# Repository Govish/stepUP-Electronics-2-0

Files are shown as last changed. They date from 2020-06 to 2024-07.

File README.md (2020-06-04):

# stepUP-Electronics-2-0
 New Electronics Suite for the stepUP 3D Printer!
 New Electronics include:
  - An updated LCD control panel loosely based off the Panelolu2
  - New printer mainboard
     - Arduino DUE printer controller running Marlin 2.0
     - ESP32 acting as WiFi server through ESP3D
     - Multiplexed SD card allowing read/write access to both the ESP32 and the Arduino DUE
     - TMC2130 Stepper Drivers with SPI configuration and connected diagnostic pins
     - RGB LED light strip control
     - High-power 20A heated bed control
     - ATX PSU control
  - Black ribbon cable wiring all throughout the machine with PCB breakouts
     - Full connectorization

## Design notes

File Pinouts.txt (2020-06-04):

 ======== LCD Connector =======
			 =========
	No Connect	-| 1   2 |- 	Ground
	Encoder B	-| 3   4 |-	LED Red
	Encoder A	-| 5   6 |-	LED Green
	Buffer SCL	-| 7   8 |-	LED Blue
	Buffer SDA	-| 9  10 |-	5V
			 =========

 ======== Encoder Daughterboard =======
			 =========
	VCC		-| 1   2 |- 	Ground
	Encoder B	-| 3   4 |-	LED Blue
	Encoder A	-| 5   6 |-	LED Green
	Encoder Switch	-| 7   8 |-	LED Red
			 =========

 ======== Y-Axis Motor/Runout Sensor Breakout ========
			 =========
	Motor 1B	-| 1   2 |-	Motor 1A
	Runout A	-| 3   4 |-	Runout B
	Motor 2B	-| 5   6 |-	Motor 2A
			 =========

 ======== Z-Axis Motor/Endstop Breakout ========
			 =========
	Motor 1B	-| 1   2 |-	Motor 1A
	Endstop A	-| 3   4 |-	Endstop B
	Motor 2B	-| 5   6 |-	Motor 2A
			 =========

 ======== LED Endstop Breakout ========
			 =========
	Blue		-| 1   2 |-	Green
	12V		-| 3   4 |-	Red
	Endstop A	-| 5   6 |-	Endstop B
			 =========

 ======== Heatbed Breakout ========
			 =========
	Thermistor A	-| 1   2 |-	Thermistor B
	Heater (-)	-| 3   4 |-	Heater (+)
	Heater (-)	-| 5   4 |-	Heater (+)
	Heater (-)	-| 7   4 |-	Heater (+)
	Heater (-)	-| 9   4 |-	Heater (+)
	Heater (-)	-| 11 12 |-	Heater (+)
	Heater (-)	-| 13 14 |-	Heater (+)
	Heater (-)	-| 15 16 |-	Heater (+)
	Heater (-)	-| 17 18 |-	Heater (+)
	Heater (-)	-| 19 20 |-	Heater (+)
	Heater (-)	-| 21 22 |-	Heater (+)
	Heater (-)	-| 23 24 |-	Heater (+)
	Heater (-)	-| 25 26 |-	Heater (+)
			 =========

 ======== Gantry Breakout (to controller) ========
			 =========
	Ext 2A		-| 1   2 |-	Ext 1A
	Ext 2B		-| 3   4 |-	Ext 1B
	+12V		-| 5   4 |-	Print Fan (-)
	+12V		-| 7   4 |-	Hotend Fan (-)
	+12V		-| 9   4 |-	Thermistor A
	Heater (-)	-| 11 12 |-	Thermistor B
	Heater (-)	-| 13 14 |-	Endstop A
	Heater (-)	-| 15 16 |-	Endstop B
	X 1B		-| 17 18 |-	X 2B
	X 1A		-| 19 20 |-	X 2A
			 =========

 ======== Gantry Breakout (to extruder) ========
			 =========
	Ext 2A		-| 1   2 |-	Ext 1A
	Ext 2B		-| 3   4 |-	Ext 1B
	Heater (-)	-| 5   4 |-	Print Fan (-)
	Heater (-)	-| 7   4 |-	Hotend Fan (-)
	Heater (-)	-| 9   4 |-	Thermistor A
	+12V		-| 11 12 |-	Thermistor B
	+12V		-| 13 14 |-	Endstop A
	+12V		-| 15 16 |-	Endstop B
			 =========

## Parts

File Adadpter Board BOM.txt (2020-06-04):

IDC-6  Connector: III
IDC-16 Connector: II
IDC-20 Connector: I
IDC-26 Connector: I

JST-4: IIIII
JST-2: IIIIIII
Screw Terminal (0.1"): I 

XT60: I
XT30: I

SMD LED: III
SMD LED RES: III

RGB ENCODER: I

USB-A Connector: I

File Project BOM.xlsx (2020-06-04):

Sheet: All Together
Package | Quantity | Price @Break | Total Price | Value | Manufacturer | Part Number | Supplier (DigiKey) P/N | Notes for Substitution | Qty on Hand | Qty to Buy | Buy Prices
Nonstandard | 4 | $0.22 | $0.88 | Fuseholder_ATM | Keystone Electronics | 3557 | 36-3557-ND | Match footprint if exists? | 0 | 5 | $1.10
02x03 P2.54mm | 6 | $0.45 | $2.70 | IDC-6 | Wurth Electronik | 61200621621 | 732-5394-ND | IDC6, Match Footprint | 0 | 7 | $3.15
02x05 P2.54mm | 1 | $0.45 | $0.45 | IDC-10 | Wurth Electronik | 61201021621 | 732-2094-ND | IDC10, Match Footprint | 0 | 2 | $0.90
02x08 P2.54mm | 2 | $0.59 | $1.18 | IDC-16 | Wurth Electronik | 61201621621 | 732-2095-ND | IDC16, Match Footprint | 0 | 3 | $1.77
02x10 P2.54mm | 2 | $0.89 | $1.78 | IDC-20 | Wurth Electronik | 61202021621 | 732-2096-ND | IDC20, Match Footprint | 0 | 3 | $2.67
02x13 P2.54mm | 2 | $1.04 | $2.08 | IDC-26 | Wurth Electronik | 61202621621 | 732-2097-ND | IDC26, Match Footprint | 0 | 3 | $3.12
Nonstandard | 1 | $1.22 | $1.22 | USB_A | CNC Tech | 1001-008B-01001 | 1175-1608-ND | Match footprint if exists? | 0 | 2 | $2.44
0603 | 5 | $0.18 | $0.90 | Red | Wurth Electronik | 150060RS55040 | 732-12015-1-ND | Match Package and Color | 0 | 6 | $1.08
0603 | 4 | $0.18 | $0.72 | Green | Wurth Electronik | 150060VS55040 | 732-12017-1-ND | Match Package and Color | 0 | 5 | $0.90
0603 | 6 | $0.18 | $1.08 | Yellow | Wurth Electronik | 150060YS55040 | 732-12018-1-ND | Match Package and Color | 0 | 7 | $1.26
1206 Reverse Mount | 1 | $0.18 | $0.18 | Red | Wurth Electronik | 156120RS75000 | 732-5030-1-ND | Match Footprint | 0 | 2 | $0.36
1206 Reverse Mount | 1 | $0.18 | $0.18 | Green | Wurth Electronik | 156120VS75000 | 732-5032-1-ND | Match Footprint | 0 | 2 | $0.36
1206 Reverse Mount | 1 | $0.18 | $0.18 | Yellow | Wurth Electronik | 156120YS75000 | 732-5034-1-ND | Match Footprint | 0 | 2 | $0.36
Nonstandard | 1 | $3.69 | $3.69 | Socket_SD | TE Connectivity AMP Connectors | 2041021-4 | A101492CT-ND | Match footprint if exists? | 0 | 2 | $7.38
TSSOP-8 4.4x3 P0.65) | 1 | $0.80 | $0.80 | 24LC256 | Microchip | 24LC256-I/ST | 24LC256-I/ST-ND | Match pinout, greater or equal capacity | 0 | 2 | $1.60
Screw_Term 2.54mm | 1 | $0.92 | $0.92 | - | TE Connectivity AMP Connectors | 282834-2 | A98333-ND | Match Pitch, Footprint | 0 | 2 | $1.84
02x05 SMD Pin Header | 1 | $0.58 | $0.58 | - | CNC Tech | 3020-10-0300-00 | 1175-1621-ND | IDC Format, Match Footprint | 0 | 1 | $0.58
02x04 P2.54mm | 1 | $2.40 | $2.40 | - | TE Connectivity AMP Connectors | 5-534998-4 | A32954-ND | 5-7mm Insulation Height | 0 | 1 | $2.40
SSOP-14 (5.3x6.2 P0.65) | 1 | $0.64 | $0.64 | 74HC4066 | Nexperia | 74HC4066DB,112 | 1727-6100-ND | Match Footprint, 4066 family | 0 | 2 | $1.28
Arduino Mega/Due | 1 | $37.40 | $37.40 | - | Arduino | A000062 | 1050-1049-ND | Requires desoldering of input DC connector (clearance) | 0 | 1 | $37.40
Nonstandard | 1 | $0.24 | $0.24 | 10A | OptiFuse | APM-10A | 2298-APM-10A-ND | Any 10A ATM Fuse | 0 | 2 | $0.48
Nonstandard | 1 | $0.24 | $0.24 | 25A | OptiFuse | APM-25A | 2298-APM-25A-ND | Any 25A ATM Fuse | 0 | 2 | $0.48
01x02 P2.5 | 8 | $0.15 | $1.20 | JST-2 | JST Sales America | B2B-XH-A(LF)(SN) | 455-2247-ND | Amazon Link (https://www.amazon.com/gp/product/B015Y6JOUG/ref=ox_sc_act_title_5?smid=AYI27JSX7SHMW&psc=1) | 20 | 0 | $0.00
01x04 P2.5 | 7 | $0.21 | $1.47 | JST-4 | JST Sales America | B4B-XH-A(LF)(SN) | 455-2249-ND | Amazon Link (https://www.amazon.com/gp/product/B015Y6JOUG/ref=ox_sc_act_title_5?smid=AYI27JSX7SHMW&psc=1) | 20 | 0 | $0.00
SMC | 1 | $0.32 | $0.32 | 80V 3A Schottky | Comchip Technology | CDBC380-G | 641-1123-1-ND | 3A, 50V Rated or more, Match Footprint | 0 | 2 | $0.64
0603 | 23 | $0.00 | $0.00 | 100n | Samsung Electromechanics | CL10B10KB8NNNC | 1276-1000-1-ND | 50V Rated X5R or better | 70 | 0 | $0.00
0603 | 1 | $0.03 | $0.03 | 270p | Samsung Electromechanics | CL10B271KB8NNNC | 1276-2019-1-ND | Check PSU design doc for voltage rating | 0 | 10 | $0.34
0603 | 1 | $0.03 | $0.03 | 4.7n | Samsung Electromechanics | CL10B472KB8NFNC | 1276-2064-1-ND | Check PSU design doc for voltage rating | 0 | 10 | $0.34
0603 | 1 | $0.04 | $0.04 | 10p | Samsung Electromechanics | CL10C100CB8NNNC | 1276-1069-1-ND | Check PSU design doc for voltage rating | 0 | 10 | $0.38
0805 | 6 | $0.00 | $0.00 | 4u7 | Samsung Electromechanics | CL21A475KPFNNNE | 1276-1259-1-ND | 10V Rated X5R or better | 9 | 0 | $0.00
SOD-123F | 33 | $0.13 | $4.42 | 50V 1A Fast Recovery | SMC Diode Solutions | DSS15UTR | 1655-1928-1-ND | >50V, 1A; Match Footprint | 0 | 40 | $5.36
CP_Radial (D12.5mm P5.00mm) | 6 | $0.24 | $1.44 | 470u | Panasonic Electronic Components | EEU-FM1H471 | P12400-ND | Match or better: voltage, high freq Iripple, impedance | 0 | 7 | $1.68
Nonstandard | 1 | $0.00 | $0.00 | - | Espressif Systems | ESP32 Core Board V2 | - | Possible pin-compatible options, match footprint | 1 | 0 | $0.00
VSSOP-8 (3.0x3.0 P0.65) | 1 | $2.14 | $2.14 | LM3488 | Texas Instruments | LM3488MMX/NOPB | 296-35417-1-ND | Different Packaging Possible | 0 | 2 | $4.28
SMDIP-4 (W9.53mm) | 3 | $0.45 | $1.35 | LTV-817S | Lite-on Inc | LTV-817S | 160-1367-5-ND | Match Footprint and Pinout; Iout > 50mA | 0 | 4 | $1.80
TSSOP-14 (4.4x5 P0.65) | 1 | $0.36 | $0.36 | 74HC14 | ON Semiconductor | MC74HC14ADTR2G | MC74HC14ADTR2GOSCT-ND | Match Footprint, 7414 family | 0 | 2 | $0.72
SSOP-28 (5.3x10.2_P0.65) | 1 | $1.26 | $1.26 | MCP23017 | Microchip Technology | MCP23017T-E/SS | MCP23017T-E/SSCT-ND | No Substitutes, but similar versions should be alright | 0 | 2 | $2.52
SOD-323 | 11 | $0.12 | $1.35 | 3.6V | ON Semiconductor | MM3Z3V6T1G | MM3Z3V6T1GOSCT-ND | Match Package and Voltage | 0 | 15 | $1.84
SOT-23 | 8 | $0.28 | $2.24 | - | ON Semiconductor | NTR3C21NZT1G | NTR3C21NZT1GOSCT-ND | >20V, >3.6A to ambient, >8V Vgs, Logic Level | 0 | 12 | $3.36
TO-252 | 4 | $0.89 | $3.56 | - | ON Semiconductor | NVD5C668NLT4G | NVD5C668NLT4GOSCT-ND | >50V, <10mOhm, <30nC gate charge, TO-252 | 0 | 6 | $5.34
SOIC-8 (3.9x4.9 P1.27) | 2 | $1.86 | $3.72 | P82B715 | Texas Instruments | P82B715DRG4 | 296-52682-1-ND | Similar part from NXP (https://www.digikey.com/product-detail/en/nxp-usa-inc/P82B715TD-112/568-3981-5-ND/739477) | 0 | 3 | $5.58
SSOP-8 (2.95x2.8 P0.65) | 1 | $0.67 | $0.67 | PCA9306 | Texas Instruments | PCA9306DCTR | 296-18509-1-ND | Match Footprint and Pinout | 0 | 2 | $1.34
2512 | 1 | $0.59 | $0.59 | 7mR | Yageo | PE2512FKE7W0R007L | YAG2161CT-ND | Match Footprint; 1% or better | 0 | 2 | $1.18
Nonstandard | 1 | $6.18 | $6.18 | RGB Encoder | Bourns | PEL12T-4225S-S1024 | PEL12T-4225S-S1024-ND | SparkFun (https://www.sparkfun.com/products/15141) | 0 | 1 | $6.18
Nonstandard | 1 | $1.06 | $1.06 | - | Murata Electronics | PKMCS0909E4000-R1 | 490-9647-1-ND | Same footprint; similar device from CUI (https://www.digikey.com/product-detail/en/CPT-9019S-SMT-TR/102-3761-1-ND/6012450) | 0 | 2 | $2.12
0603 | 1 | $0.01 | $0.01 | 100R | Yageo | RC0603FR-07100RL | 311-100HRCT-ND | Match Footprint; 1% or better | 0 | 100 | $0.94
0603 | 34 | $0.00 | $0.00 | 10k | Yageo | RC0603FR-0710KL | 311-10.0KHRCT-ND | Match Footprint; 1% or better | 70 | 0 | $0.00
0603 | 3 | $0.02 | $0.07 | 16.9k | Yageo | RC0603FR-0716K9L | 311-16.9KHRCT-ND | Match Footprint; 1% or better | 0 | 10 | $0.23
0603 | 26 | $0.00 | $0.00 | 1k | Yageo | RC0603FR-071KL | 311-1.00KHRCT-ND | Match Footprint; 1% or better | 70 | 0 | $0.00
0603 | 1 | $0.02 | $0.02 | 22.6k | Yageo | RC0603FR-0722K6L | 311-22.6KHRCT-ND | Match Footprint; 1% or better | 0 | 10 | $0.23
0603 | 9 | $0.00 | $0.00 | 240k | Yageo | RC0603FR-07240KL | 311-240KHRCT-ND | Match Footprint; 1% or better | 70 | 0 | $0.00
0603 | 3 | $0.01 | $0.03 | 2k | Yageo | RC0603FR-072KL | 311-2.00KHRCT-ND | Match Package, 1% or better | 0 | 100 | $0.94
0603 | 18 | $0.00 | $0.00 | 390R | Yageo | RC0603FR07390RL | 311-390HRCT-ND | Match Footprint; 1% or better | 70 | 0 | $0.00
0603 | 11 | $0.01 | $0.10 | 4k7 | Yageo | RC0603FR-074K7L | 311-4.70KHRCT-ND | Match Footprint; 1% or better | 0 | 100 | $0.94
0603 | 3 | $0.26 | $0.77 | 0R | Yageo | RC0603JR-070RL | 311-0.0GRCT-ND | Match Footprint | 0 | 0 | $0.00
5050-6 | 1 | $1.37 | $1.37 | RGB | Rohm Semiconductor | SMLVN6RGB1U1 | 846-1206-1-ND | Messed up footprint, make whatever work | 0 | 2 | $2.74
SSOP-20 (5.3x7.2 P0.65) | 2 | $0.39 | $0.78 | 74HC245 | Texas Instruments | SN74HC245DBR | 296-8277-1-ND | Match Footprints, 74245 Family, NONINVERTING | 0 | 3 | $1.17
SC70-6 | 1 | $0.36 | $0.36 | - | Texas Instruments | SN74LVC1G3157DCK3 | 296-SN74LVC1G3157DCK3-ND | Match Footprint and Pinout | 0 | 2 | $0.72
Nonstandard | 1 | $1.25 | $1.25 | 4.7uH | Bourns Inc. | SRR1260-4R7Y | SRR1260-4R7YCT-ND | Check PSU design doc for ratings, match footprint | 0 | 2 | $2.50
MSOP-8 (3x3 P0.65) | 1 | $0.86 | $0.86 | LM393 | Texas Instruments | TLV7032DGKR | 296-TLV7032DGKRCT-ND | Match Pinout, 5V operation, PUSH-PULL OUTPUT | 0 | 2 | $1.72
StepStick | 4 | $8.25 | $32.99 | StepStick-TMC2130 | Waterott Electronics | TMC2130 SilentStepStick | - | Amazon Link (https://www.amazon.com/gp/product/B07RSX2W3V) | 4 | 0 | $0.00
TSSOP-24 (4.4x7.8 P0.65) | 1 | $1.56 | $1.56 | - | Texas Instruments | TS3A27518EPWR | 296-24570-1-ND | Different Packaging Possible | 0 | 2 | $3.12
Nonstandard | 1 | $1.87 | $1.87 | 10k | Vishay Sfernice | TS53YJ103MR10 | TS53YJ-10KCT-ND | 10K; Match Footprint | 0 | 2 | $3.74
02x04 SMD Pin Header | 1 | $0.98 | $0.98 | - | Samtec | TSM-104-03-L-DV | SAM12226-ND | 10.5mm or taller; Match Footprint | 0 | 2 | $1.96
01x18 SMD Pin Header | 1 | $1.60 | $1.60 | - | Samtec | TSM-120-02-T-SV | SAM12274-ND | Should be >10.5mm from board to tip of connector | 0 | 2 | $3.20
USB_B | 1 | $0.54 | $0.54 | USB_B | CUI Devices | UJ2-BH-W1-TH | 102-5887-ND | Match Footprint | 0 | 2 | $1.08
XT30 | 1 | $7.95 | $7.95 | XT30-Female | Changzhou Amass | XT30U-F | - | Amazon Link (https://www.amazon.com/Geesatis-Yellow-Connectors-Battery-Connector/dp/B07Z4G6BVM?s=electronics) | 3 | 0 | $0.00
XT60 | 1 | $8.99 | $8.99 | XT60-Female | Changzhou Amass | XT60-F | - | Amazon Link (https://www.amazon.com/Finware-Female-Bullet-Connectors-Battery/dp/B01ETROGP4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) | 10 | 0 | $0.00
XT60 | 1 | $0.00 | $0.00 | XT60 Male | Changzhou Amass | XT60-M | - | Amazon Link (https://www.amazon.com/Finware-Female-Bullet-Connectors-Battery/dp/B01ETROGP4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) | 10 | 0 | $0.00
 |  |  |  |  |  |  |  | TOTAL BOM COST |  |  | $143.15

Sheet: stepUP LCD
stepUP LCD Bill of Materials
LAST UPDATED 3/30/2020
Reference Number | Package | Quantity | Price @Break | Total Price | Value | Manufacturer | Part Number | Supplier (DigiKey) P/N | Notes for Substitution | Qty on Hand | Qty to Buy
BZ1 | Nonstandard | 1 | $1.06 | $1.06 | - | Murata Electronics | PKMCS0909E4000-R1 | 490-9647-1-ND | Same footprint; similar device from CUI (https://www.digikey.com/product-detail/en/CPT-9019S-SMT-TR/102-3761-1-ND/6012450) | 0 | 2
C2, C3 | 0603 | 2 | $0.00 | $0.00 | 100n | Samsung Electromechanics | CL10B10KB8NNNC | 1276-1000-1-ND | 50V Rated X5R or better | 70 | 0
D1 | 1206 Reverse Mount | 1 | $0.18 | $0.18 | Red | Wurth Electronik | 156120RS75000 | 732-5030-1-ND | Match Footprint | 0 | 2
D2 | 1206 Reverse Mount | 1 | $0.18 | $0.18 | Yellow | Wurth Electronik | 156120YS75000 | 732-5034-1-ND | Match Footprint | 0 | 2
D3 | 1206 Reverse Mount | 1 | $0.18 | $0.18 | Green | Wurth Electronik | 156120VS75000 | 732-5032-1-ND | Match Footprint | 0 | 2
J1 | 02x05 SMD Pin Header | 1 | $0.58 | $0.58 | - | CNC Tech | 3020-10-0300-00 | 1175-1621-ND | IDC Format, Match Footprint | 0 | 2
J2 | 02x04 SMD Pin Header | 1 | $0.98 | $0.98 | - | Samtec | TSM-104-03-L-DV | SAM12226-ND | 10.5mm or taller; Match Footprint | 0 | 2
J3 | 01x18 SMD Pin Header | 1 | $1.60 | $1.60 | - | Samtec | TSM-120-02-T-SV | SAM12274-ND | Should be >10.5mm from board to tip of connector | 0 | 2
R1, R3 | 0603 | 2 | $0.01 | $0.02 | 4k7 | Yageo | RC0603FR-074K7L | 311-4.70KHRCT-ND | Match Footprint; 1% or better | 0 | 100
R2 | 0603 | 1 | $0.00 | $0.00 | 10k | Yageo | RC0603FR-0710KL | 311-10.0KHRCT-ND | Match Footprint; 1% or better | 70 | 0
R4, R5, R6 | 0603 | 3 | $0.26 | $0.77 | 0R |  | RC0603JR-070RL | 311-0.0GRCT-ND | Match Footprint | 0 | 0
R7, R8, R9, R10, R11, R12 | 0603 | 6 | $0.00 | $0.00 | 390R | Yageo | RC0603FR07390RL | 311-390HRCT-ND | Match Footprint; 1% or better | 70 | 0
R101, R102 | 0603 | 2 | $0.00 | $0.00 | 1k | Yageo | RC0603FR-071KL | 311-1.00KHRCT-ND | Match Footprint; 1% or better | 70 | 0
RV1 | Nonstandard | 1 | $1.87 | $1.87 | 10k | Vishay Sfernice | TS53YJ103MR10 | TS53YJ-10KCT-ND | 10K; Match Footprint | 0 | 2
U2 | SOIC-8 (3.9x4.9_P1.27) | 1 | $1.86 | $1.86 | P82B715 | Texas Instruments | P82B715DRG4 | 296-52682-1-ND | Similar part from NXP (https://www.digikey.com/product-detail/en/nxp-usa-inc/P82B715TD-112/568-3981-5-ND/739477) | 0 | 2
U3 | SSOP-28 (5.3x10.2_P0.65) | 1 | $1.26 | $1.26 | MCP23017 | Microchip Technology | MCP23017T-E/SS | MCP23017T-E/SSCT-ND | No Substitutes, but similar versions should be alright | 0 | 2
 |  |  | TOTAL BOM COST | $10.54

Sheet: Breakout Boards
stepUP Adapter Boards
LAST UPDATED 3/30/2020
Package | Quantity | Price @Break | Total Price | Value | Manufacturer | Part Number | Supplier (DigiKey) P/N | Notes for Substitution | Qty on Hand | Qty to Buy
02x03 P2.54mm | 3 | $0.45 | $1.35 | IDC-6 | Wurth Electronik | 61200621621 | 732-5394-ND | IDC6, Match Footprint | 0 | 4
02x08 P2.54mm | 2 | $0.59 | $1.18 | IDC-16 | Wurth Electronik | 61201621621 | 732-2095-ND | IDC16, Match Footprint | 0 | 3
02x10 P2.54mm | 1 | $0.89 | $0.89 | IDC-20 | Wurth Electronik | 61202021621 | 732-2096-ND | IDC20, Match Footprint | 0 | 2
02x13 P2.54mm | 1 | $1.04 | $1.04 | IDC-26 | Wurth Electronik | 61202621621 | 732-2097-ND | IDC26, Match Footprint | 0 | 2
01x04 P2.5 | 5 | $0.21 | $1.05 | JST-4 | JST Sales America | B4B-XH-A(LF)(SN) | 455-2249-ND | Amazon Link (https://www.amazon.com/gp/product/B015Y6JOUG/ref=ox_sc_act_title_5?smid=AYI27JSX7SHMW&psc=1) | 20 | 0
01x02 P2.5 | 7 | $0.15 | $1.05 | JST-2 | JST Sales America | B2B-XH-A(LF)(SN) | 455-2247-ND | Amazon Link (https://www.amazon.com/gp/product/B015Y6JOUG/ref=ox_sc_act_title_5?smid=AYI27JSX7SHMW&psc=1) | 20 | 0
Screw_Term 2.54mm | 1 | $0.92 | $0.92 | - | TE Connectivity AMP Connectors | 282834-2 | A98333-ND | Match Pitch, Footprint | 0 | 2
XT30 | 1 | $7.95 | $7.95 | XT30-Female | Changzhou Amass | XT30U-F | - | Amazon Link (https://www.amazon.com/Geesatis-Yellow-Connectors-Battery-Connector/dp/B07Z4G6BVM?s=electronics) | 3 | 0
XT60 | 1 | $8.99 | $8.99 | XT60-Female | Changzhou Amass | XT60-F | - | Amazon Link (https://www.amazon.com/Finware-Female-Bullet-Connectors-Battery/dp/B01ETROGP4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) | 10 | 0
Nonstandard | 1 | $6.18 | $6.18 | RGB Encoder | Bourns | PEL12T-4225S-S1024 | PEL12T-4225S-S1024-ND | SparkFun (https://www.sparkfun.com/products/15141) | 0 | 2
02x04 P2.54mm | 1 | $2.40 | $2.40 | - | TE Connectivity AMP Connectors | 5-534998-4 | A32954-ND | 5-7mm Insulation Height | 0 | 2
0603 | 1 | $0.18 | $0.18 | Red | Wurth Electronik | 150060RS55040 | 732-12015-1-ND | Match Package and Color | 0 | 2
0603 | 1 | $0.18 | $0.18 | Yellow | Wurth Electronik | 150060YS55040 | 732-12018-1-ND | Match Package and Color | 0 | 2
0603 | 1 | $0.18 | $0.18 | Green | Wurth Electronik | 150060VS55040 | 732-12017-1-ND | Match Package and Color | 0 | 2
0603 | 3 | $0.01 | $0.03 | 2k | Yageo | RC0603FR-072KL | 311-2.00KHRCT-ND | Match Package, 1% or better | 0 | 100
Nonstandard | 1 | $1.22 | $1.22 | USB-A | CNC Tech | 1001-008B-01001 | 1175-1608-ND | Match Footprint | 0 | 2
 |  | TOTAL BOM COST | $34.79

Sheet: Quickstep
Quickstep Controller Bill of Materials
LAST UPDATED 3/30/2020
Reference Number | Package | Quantity | Price @Break | Total Price | Value | Manufacturer | Part Number | Supplier (DigiKey) P/N | Notes for Substitution | Qty on Hand
C201, C202, C203, C401, C402, C403, C404, C405, C406, C407, C408, C501, C502, C709, C801, C803, C804, C807, C809, C1201, C1202 | 0603 | 21 | $0.00 | $0.00 | 100n | Samsung Electromechanics | CL10B10KB8NNNC | 1276-1000-1-ND | 50V Rated X5R or better | 70
C301, C302, C701, C703, C705, C707 | 0805 | 6 | $0.00 | $0.00 | 4u7 | Samsung Electromechanics | CL21A475KPFNNNE | 1276-1259-1-ND | 10V Rated X5R or better | 9
C702, C704, C706, C708, C802, C810 | CP_Radial (D12.5mm P5.00mm) | 6 | $0.24 | $1.44 | 470u | Panasonic Electronic Components | EEU-FM1H471 | P12400-ND | Match or better: voltage, high freq Iripple, impedance | 0
C805 | 0603 | 1 | $0.03 | $0.03 | 270p | Samsung Electromechanics | CL10B271KB8NNNC | 1276-2019-1-ND | Check PSU design doc for voltage rating | 0
C806 | 0603 | 1 | $0.03 | $0.03 | 4.7n | Samsung Electromechanics | CL10B472KB8NFNC | 1276-2064-1-ND | Check PSU design doc for voltage rating | 0
C808 | 0603 | 1 | $0.04 | $0.04 | 10p | Samsung Electromechanics | CL10C100CB8NNNC | 1276-1069-1-ND | Check PSU design doc for voltage rating | 0
D201, D302, D410, D702 | 0603 | 4 | $0.18 | $0.72 | Red | Wurth Electronik | 150060RS55040 | 732-12015-1-ND | Match Package and Color | 0
D202, D409, D703 | 0603 | 3 | $0.18 | $0.54 | Green | Wurth Electronik | 150060VS55040 | 732-12017-1-ND | Match Package and Color | 0
D301, D405, D406, D407, D408 | 0603 | 5 | $0.18 | $0.90 | Yellow | Wurth Electronik | 150060YS55040 | 732-12018-1-ND | Match Package and Color | 0
D303, D304, D401, D402, D403, D404, D411, D412, D413, D1201, D1202 | SOD-323 | 11 | $0.12 | $1.35 | 3.6V | ON Semiconductor | MM3Z3V6T1G | MM3Z3V6T1GOSCT-ND | Match Package and Voltage | 0
D501 | 5050-6 | 1 | $1.37 | $1.37 | RGB | Rohm Semiconductor | SMLVN6RGB1U1 | 846-1206-1-ND | Messed up footprint, make whatever work | 0
D701, D901, D902, D903, D904, D905, D906, D907, D908, D1001, D1002, D1003, D1004, D1005, D1006, D1007, D1008, D1401, D1402, D1403, D1404, D1405, D1406, D1407, D1408, D1409, D1410, D1411, D1412, D1413, D1414, D1415, D1416 | SOD-123F | 33 | $0.13 | $4.42 | 50V 1A Fast Recovery | SMC Diode Solutions | DSS15UTR | 1655-1928-1-ND | >50V, 1A; Match Footprint | 0
D801 | SMC | 1 | $0.32 | $0.32 | 80V 3A Schottky | Comchip Technology | CDBC380-G | 641-1123-1-ND | 3A, 50V Rated or more, Match Footprint | 0
F1501 | Nonstandard | 1 | $0.24 | $0.24 | 10A | OptiFuse | APM-10A | 2298-APM-10A-ND | Any 10A ATM Fuse | 0
F1502 | Nonstandard | 1 | $0.24 | $0.24 | 25A | OptiFuse | APM-25A | 2298-APM-25A-ND | Any 25A ATM Fuse | 0
F1501, F1502 | Nonstandard | 4 | $0.22 | $0.88 | Fuseholder_ATM | Keyston Electronics | 3557 | 36-3557-ND | Match footprint if exists? | 0
J101, J1502 | 01x04 P2.5mm | 2 | $0.21 | $0.42 | JST-4 | JST Sales America | B4B-XH-A(LF)(SN) | 455-2249-ND | Amazon Link (https://www.amazon.com/gp/product/B015Y6JOUG/ref=ox_sc_act_title_5?smid=AYI27JSX7SHMW&psc=1) | 20
J201 | Nonstandard | 1 | $3.69 | $3.69 | Socket_SD | TE Connectivity AMP Connectors | 2041021-4 | A101492CT-ND | Match footprint if exists? | 0
J601 | Nonstandard | 1 | $1.22 | $1.22 | USB_A | CNC Tech | 1001-008B-01001 | 1175-1608-ND | Match footprint if exists? | 0
J602 | USB_B | 1 | $0.54 | $0.54 | USB_B | CUI Devices | UJ2-BH-W1-TH | 102-5887-ND | Match Footprint | 0
J901, J1001, J1301 | 02x03 P2.54mm | 3 | $0.45 | $1.35 | IDC-6 | Wurth Electronik | 61200621621 | 732-5394-ND | IDC6, Match Footprint | 0
J1101 | 02x13 P2.54mm | 1 | $1.04 | $1.04 | IDC-26 | Wurth Electronik | 61202621621 | 732-2097-ND | IDC26, Match Footprint | 0
J1201 | 02x05 P2.54mm | 1 | $0.45 | $0.45 | IDC-10 | Wurth Electronik | 61201021621 | 732-2094-ND | IDC10, Match Footprint | 0
J1401 | 02x10 P2.54mm | 1 | $0.89 | $0.89 | IDC-20 | Wurth Electronik | 61202021621 | 732-2096-ND | IDC20, Match Footprint | 0
J1501 | 01x02 P2.5mm | 1 | $0.15 | $0.15 | JST-2 | JST Sales America | B2B-XH-A(LF)(SN) | 455-2247-ND | Amazon Link (https://www.amazon.com/gp/product/B015Y6JOUG/ref=ox_sc_act_title_5?smid=AYI27JSX7SHMW&psc=1) | 20
J1503 | XT60 | 1 | $0.00 | $0.00 | XT60 Male | Changzhou Amass | XT60-M | - | Amazon Link (https://www.amazon.com/Finware-Female-Bullet-Connectors-Battery/dp/B01ETROGP4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) | 10
L801 | Nonstandard | 1 | $1.25 | $1.25 | 4.7uH | Bourns Inc. | SRR1260-4R7Y | SRR1260-4R7YCT-ND | Check PSU design doc for ratings, match footprint | 0
Q301, Q302, Q304, Q802 | TO-252 | 4 | $0.89 | $3.56 | - | ON Semiconductor | NVD5C668NLT4G | NVD5C668NLT4GOSCT-ND | >50V, <10mOhm, <30nC gate charge, TO-252 | 0
Q303, Q401, Q402, Q501, Q502, Q503, Q701, Q801 | SOT-23 | 8 | $0.28 | $2.24 | - | ON Semiconductor | NTR3C21NZT1G | NTR3C21NZT1GOSCT-ND | >20V, >3.6A to ambient, >8V Vgs, Logic Level | 0
R201, R202, R301, R302, R409, R410, R411, R412, R413, R417, R418, R419, R420, R421, R514, R515, R516, R712, R715, R803, R805, R807, R808, R816 | 0603 | 24 | $0.00 | $0.00 | 1k | Yageo | RC0603FR-071KL | 311-1.00KHRCT-ND | Match Footprint; 1% or better | 70
R203, R204, R205, R206, R207, R208, R209, R401, R402, R403, R404, R405, R406, R407, R408, R414, R701, R702, R703, R704, R705, R706, R707, R708, R710, R713, R714, R804, R809, R810, R811, R1201, R1202 | 0603 | 33 | $0.00 | $0.00 | 10k | Yageo | RC0603FR-0710KL | 311-10.0KHRCT-ND | Match Footprint; 1% or better | 70
R303, R304, R306, R311, R312, R506, R507, R508, R509, R510, R709, R711 | 0603 | 12 | $0.00 | $0.00 | 390R | Yageo | RC0603FR-07390RL | 311-390HRCT-ND | Match Footprint; 1% or better | 70
R305, R307, R308, R415, R416, R503, R511, R512, R513 | 0603 | 9 | $0.00 | $0.00 | 240k | Yageo | RC0603FR-07240KL | 311-240KHRCT-ND | Match Footprint; 1% or better | 70
R309, R310, R313, R314, R501, R502, R504, R505, R802 | 0603 | 9 | $0.01 | $0.08 | 4k7 | Yageo | RC0603FR-074K7L | 311-4.70KHRCT-ND | Match Footprint; 1% or better | 0
R801, R806, R812 | 0603 | 3 | $0.02 | $0.07 | 16.9k | Yageo | RC0603FR-0716K9L | 311-16.9KHRCT-ND | Match Footprint; 1% or better | 0
R813 | 0603 | 1 | $0.01 | $0.01 | 100R | Yageo | RC0603FR-07100RL | 311-100HRCT-ND | Match Footprint; 1% or better | 0
R814 | 2512 | 1 | $0.59 | $0.59 | 7mR | Yageo | PE2512FKE7W0R007L | YAG2161CT-ND | Match Footprint; 1% or better | 0
R815 | 0603 | 1 | $0.02 | $0.02 | 22.6k |  | RC0603FR-0722K6L | 311-22.6KHRCT-ND | Match Footprint; 1% or better | 0
U201 | TSSOP-24 (4.4x7.8 P0.65) | 1 | $1.56 | $1.56 | - | Texas Instruments | TS3A27518EPWR | 296-24570-1-ND | Different Packaging Possible | 0
U202 | SC70-6 | 1 | $0.36 | $0.36 | - | Texas Instruments | SN74LVC1G3157DCK3 | 296-SN74LVC1G3157DCK3-ND | Match Footprint and Pinout | 0
U301, U302, U708 | SMDIP-4 (W9.53mm) | 3 | $0.45 | $1.35 | LTV-817S | Lite-on Inc | LTV-817S | 160-1367-5-ND | Match Footprint and Pinout; Iout > 50mA | 0
U401 | TSSOP-14 (4.4x5 P0.65) | 1 | $0.36 | $0.36 | 74HC14 | ON Semiconductor | MC74HC14ADTR2G | MC74HC14ADTR2GOSCT-ND | Match Footprint, 7414 family | 0
U501 | SSOP-8 (2.95x2.8 P0.65) | 1 | $0.67 | $0.67 | PCA9306 | Texas Instruments | PCA9306DCTR | 296-18509-1-ND | Match Footprint and Pinout | 0
U502 | SOIC-8 (3.9x4.9 P1.27) | 1 | $1.86 | $1.86 | P82B715 | Texas Instruments | P82B715DRG4 | 296-52682-1-ND | Similar part from NXP (https://www.digikey.com/product-detail/en/nxp-usa-inc/P82B715TD-112/568-3981-5-ND/739477) | 0
U503 | TSSOP-8 4.4x3 P0.65) | 1 | $0.80 | $0.80 | 24LC256 | Microchip | 24LC256-I/ST | 24LC256-I/ST-ND | Match pinout, greater or equal capacity | 0
U601 | Nonstandard | 1 | $0.00 | $0.00 | - | Espressif Systems | ESP32 Core Board V2 | - | Possible pin-compatible options, match footprint | 1
U701, U702, U703, U704 | StepStick | 4 | $8.25 | $32.99 | StepStick-TMC2130 | Waterott Electronics | TMC2130 SilentStepStick | - | Amazon Link (https://www.amazon.com/gp/product/B07RSX2W3V) | 0
U705 | SSOP-14 (5.3x6.2 P0.65) | 1 | $0.64 | $0.64 | 74HC4066 | Nexperia | 74HC4066DB,112 | 1727-6100-ND | Match Footprint, 4066 family | 0
U706, U707 | SSOP-20 (5.3x7.2 P0.65) | 2 | $0.39 | $0.78 | 74HC245 | Texas Instruments | SN74HC245DBR | 296-8277-1-ND | Match Footprints, 74245 Family, NONINVERTING | 0
U801 | VSSOP-8 (3.0x3.0 P0.65) | 1 | $2.14 | $2.14 | LM3488 | Texas Instruments | LM3488MMX/NOPB | 296-35417-1-ND | Different Packaging Possible | 0
U802 | MSOP-8 (3x3 P0.65) | 1 | $0.86 | $0.86 | LM393 | Texas Instruments | TLV7032DGKR | 296-TLV7032DGKRCT-ND | Match Pinout, 5V operation, PUSH-PULL OUTPUT | 0
XA601 | Arduino Mega/Due | 1 | $37.40 | $37.40 | - | Arduino | A000062 | 1050-1049-ND | Requires desoldering of input DC connector (clearance) | 0
 |  |  | TOTAL BOM COST | $111.88

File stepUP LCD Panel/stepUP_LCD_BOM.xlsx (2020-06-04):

stepUP LCD Bill of Materials
LAST UPDATED 9/25/2019
Reference Number | Package | Quantity | Price @Break | Total Price | Value | Manufacturer | Part Number | Supplier (DigiKey) P/N | Notes for Substitution | Qty on Hand
BZ1 | Nonstandard | 1 |  | $0.00 | -
C2, C3 | 0603 | 2 |  | $0.00 | 100n
D1 | 1206 Reverse Mount | 1 |  | $0.00 | Red
D2 | 1206 Reverse Mount | 1 |  | $0.00 | Yellow
D3 | 1206 Reverse Mount | 1 |  | $0.00 | Green
J1 | 02x05 SMD Pin Header | 1 |  | $0.00 | -
J2 | 02x04 SMD Pin Header | 1 |  | $0.00 | -
J3 | 01x18 SMD Pin Header | 1 |  | $0.00 | -
R1, R3 | 0603 | 2 |  | $0.00 | 4k7
R2 | 0603 | 1 |  | $0.00 | 10k
R4, R5, R6 | 0603 | 3 |  | $0.00 | 0R
R7, R8, R9, R10, R11, R12 | 0603 | 6 |  | $0.00 | 390R
R101, R102 | 0603 | 2 |  | $0.00 | 1k
RV1 | Nonstandard | 1 |  | $0.00 | R_POT
U2 | SOIC-8 (3.9x4.9_P1.27) | 1 |  | $0.00 | P82B715
U3 | SSOP-28 (5.3x10.2_P0.65) | 1 |  | $0.00 | MCP23017

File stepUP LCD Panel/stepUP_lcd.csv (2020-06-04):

Item | Qty | Reference(s) | Value | LibPart | Footprint | Datasheet
1 | 1 | BZ1 | Buzzer | Device:Buzzer | Custom-Electromechanical:Buzzer_CUI_CPT9019S | ~
2 | 2 | C2, C3 | 100n | Device:C | Capacitor_SMD:C_0603_1608Metric_Pad1.05x0.95mm_HandSolder | ~
3 | 3 | D1, D2, D3 | LED | Device:LED | Custom-DiscreteSemi:LED_1206ReverseMount | ~
4 | 1 | G101 | Stepper Icon | Custom-Misc:Graphic_Placeholder | Custom-Graphics:Icon_Stepper
5 | 1 | G102 | SD Icon | Custom-Misc:Graphic_Placeholder | Custom-Graphics:Icon_SD
6 | 1 | G103 | Hot Icon | Custom-Misc:Graphic_Placeholder | Custom-Graphics:Icon_Temp
7 | 1 | H1 | MountingHole | Mechanical:MountingHole | Custom-Mechanical:RGB_Encoder_Hole | ~
8 | 5 | H2, H3, H4, H5, H6 | MountingHole | Mechanical:MountingHole | MountingHole:MountingHole_5.3mm_M5_Pad | ~
9 | 9 | H7, H8, H9, H10, H11, H12, H13, H14, H15 | MountingHole | Mechanical:MountingHole | MountingHole:MountingHole_3.2mm_M3_Pad | ~
10 | 1 | J1 | Conn_02x05_Odd_Even | Connector_Generic:Conn_02x05_Odd_Even | Custom-Electromechanical:PinHeader_2x05_P2.54mm_Shrouded | ~
11 | 1 | J2 | Conn_02x04_Odd_Even | Connector_Generic:Conn_02x04_Odd_Even | Connector_PinHeader_2.54mm:PinHeader_2x04_P2.54mm_Vertical_SMD | ~
12 | 1 | J3 | Conn_01x18 | Connector_Generic:Conn_01x18 | Connector_PinHeader_2.54mm:PinHeader_1x18_P2.54mm_Vertical_SMD_Pin1Left | ~
13 | 2 | R1, R3 | 4K7 | Device:R | Resistor_SMD:R_0603_1608Metric_Pad1.05x0.95mm_HandSolder | ~
14 | 1 | R2 | 10K | Device:R | Resistor_SMD:R_0603_1608Metric_Pad1.05x0.95mm_HandSolder | ~
15 | 3 | R4, R5, R6 | 0R | Device:R | Resistor_SMD:R_0603_1608Metric_Pad1.05x0.95mm_HandSolder | ~
16 | 6 | R7, R8, R9, R10, R11, R12 | 390R | Device:R | Resistor_SMD:R_0603_1608Metric_Pad1.05x0.95mm_HandSolder | ~
17 | 2 | R101, R102 | 1K | Device:R | Resistor_SMD:R_0603_1608Metric_Pad1.05x0.95mm_HandSolder | ~
18 | 1 | RV1 | R_POT | Device:R_POT | Custom-Electromechanical:Potentiometer_Vishay_TS53YJ | ~
19 | 1 | U2 | P82B715 | Custom-InterfaceIC:P82B715 | Package_SO:SOIC-8_3.9x4.9mm_P1.27mm | http://www.ti.com/lit/ds/symlink/p82b715.pdf
20 | 1 | U3 | MCP23017_SS | Interface_Expansion:MCP23017_SS | Package_SO:SSOP-28_5.3x10.2mm_P0.65mm | http://ww1.microchip.com/downloads/en/DeviceDoc/20001952C.pdf

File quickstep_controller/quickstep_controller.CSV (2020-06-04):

Source: | D:\Documents\Projects\stepUP Electronics 2-0\quickstep_controller\quickstep_controller\quickstep_controller.sch
Date: | 3/30/2020 3:14
Tool: | Eeschema (5.1.4)-1
Generator: | C:\Program Files\KiCad\bin\scripting\plugins/bom_csv_grouped_by_value.py
Component Count: | 252
Individual Components:
Item | Qty | Reference(s) | Value | LibPart | Footprint | Datasheet | P/N: | Part No. | Part No.
 |  | C201 | 100n | Device:C | Capacitor_SMD:C_0603_1608Metric_Pad1.05x0.95mm_HandSolder | ~
 |  | C202 | 100n | Device:C | Capacitor_SMD:C_0603_1608Metric_Pad1.05x0.95mm_HandSolder | ~
 |  | C203 | 100n | Device:C | Capacitor_SMD:C_0603_1608Metric_Pad1.05x0.95mm_HandSolder | ~
 |  | C301 | 4u7 | Device:C | Capacitor_SMD:C_0805_2012Metric_Pad1.15x1.40mm_HandSolder | ~
 |  | C302 | 4u7 | Device:C | Capacitor_SMD:C_0805_2012Metric_Pad1.15x1.40mm_HandSolder | ~
 |  | C401 | 100n | Device:C | Capacitor_SMD:C_0603_1608Metric_Pad1.05x0.95mm_HandSolder | ~
 |  | C402 | 100n | Device:C | Capacitor_SMD:C_0603_1608Metric_Pad1.05x0.95mm_HandSolder | ~
 |  | C403 | 100n | Device:C | Capacitor_SMD:C_0603_1608Metric_Pad1.05x0.95mm_HandSolder | ~
 |  | C404 | 100n | Device:C | Capacitor_SMD:C_0603_1608Metric_Pad1.05x0.95mm_HandSolder | ~
 |  | C405 | 100n | Device:C | Capacitor_SMD:C_0603_1608Metric_Pad1.05x0.95mm_HandSolder | ~
 |  | C406 | 100n | Device:C | Capacitor_SMD:C_0603_1608Metric_Pad1.05x0.95mm_HandSolder | ~
 |  | C407 | 100n | Device:C | Capacitor_SMD:C_0603_1608Metric_Pad1.05x0.95mm_HandSolder | ~
 |  | C408 | 100n | Device:C | Capacitor_SMD:C_0603_1608Metric_Pad1.05x0.95mm_HandSolder | ~
 |  | C501 | 100n | Device:C | Capacitor_SMD:C_0603_1608Metric_Pad1.05x0.95mm_HandSolder | ~
 |  | C502 | 100n | Device:C | Capacitor_SMD:C_0603_1608Metric_Pad1.05x0.95mm_HandSolder | ~
 |  | C701 | 4u7 | Device:C | Capacitor_SMD:C_0805_2012Metric_Pad1.15x1.40mm_HandSolder | ~
 |  | C702 | 470u | Device:CP1 | Capacitor_THT:CP_Radial_D12.5mm_P5.00mm | ~ |  | EEU-FM1H471
 |  | C703 | 4u7 | Device:C | Capacitor_SMD:C_0805_2012Metric_Pad1.15x1.40mm_HandSolder | ~
 |  | C704 | 470u | Device:CP1 | Capacitor_THT:CP_Radial_D12.5mm_P5.00mm | ~ |  | EEU-FM1H471
 |  | C705 | 4u7 | Device:C | Capacitor_SMD:C_0805_2012Metric_Pad1.15x1.40mm_HandSolder | ~
 |  | C706 | 470u | Device:CP1 | Capacitor_THT:CP_Radial_D12.5mm_P5.00mm | ~ |  | EEU-FM1H471
 |  | C707 | 4u7 | Device:C | Capacitor_SMD:C_0805_2012Metric_Pad1.15x1.40mm_HandSolder | ~
 |  | C708 | 470u | Device:CP1 | Capacitor_THT:CP_Radial_D12.5mm_P5.00mm | ~ |  | EEU-FM1H471
 |  | C709 | 100n | Device:C | Capacitor_SMD:C_0603_1608Metric_Pad1.05x0.95mm_HandSolder | ~
 |  | C801 | 100n | Device:C | Capacitor_SMD:C_0603_1608Metric_Pad1.05x0.95mm_HandSolder | ~
 |  | C802 | 470u | Device:CP1 | Capacitor_THT:CP_Radial_D12.5mm_P5.00mm | ~ |  | EEU-FM1H471
 |  | C803 | 100n | Device:C | Capacitor_SMD:C_0603_1608Metric_Pad1.05x0.95mm_HandSolder | ~
 |  | C804 | 100n | Device:C | Capacitor_SMD:C_0603_1608Metric_Pad1.05x0.95mm_HandSolder | ~
 |  | C805 | 270p | Device:C | Capacitor_SMD:C_0603_1608Metric_Pad1.05x0.95mm_HandSolder | ~
 |  | C806 | 4.7n | Device:C | Capacitor_SMD:C_0603_1608Metric_Pad1.05x0.95mm_HandSolder | ~
 |  | C807 | 100n | Device:C | Capacitor_SMD:C_0603_1608Metric_Pad1.05x0.95mm_HandSolder | ~
 |  | C808 | 10p | Device:C | Capacitor_SMD:C_0603_1608Metric_Pad1.05x0.95mm_HandSolder | ~
 |  | C809 | 100n | Device:C | Capacitor_SMD:C_0603_1608Metric_Pad1.05x0.95mm_HandSolder | ~
 |  | C810 | 470u | Device:CP1 | Capacitor_THT:CP_Radial_D12.5mm_P5.00mm | ~ |  | EEU-FM1H471
 |  | C1201 | 100n | Device:C | Capacitor_SMD:C_0603_1608Metric_Pad1.05x0.95mm_HandSolder | ~
 |  | C1202 | 100n | Device:C | Capacitor_SMD:C_0603_1608Metric_Pad1.05x0.95mm_HandSolder | ~
 |  | D201 | RED | Device:LED | LED_SMD:LED_0603_1608Metric_Pad1.05x0.95mm_HandSolder | ~
 |  | D202 | GREEN | Device:LED | LED_SMD:LED_0603_1608Metric_Pad1.05x0.95mm_HandSolder | ~
 |  | D301 | YELLOW | Device:LED | LED_SMD:LED_0603_1608Metric_Pad1.05x0.95mm_HandSolder | ~
 |  | D302 | RED | Device:LED | LED_SMD:LED_0603_1608Metric_Pad1.05x0.95mm_HandSolder | ~
 |  | D303 | 3.6V | Device:D_Zener | Diode_SMD:D_SOD-323_HandSoldering | ~ |  | MM3Z3V6T1G
 |  | D304 | 3.6V | Device:D_Zener | Diode_SMD:D_SOD-323_HandSoldering | ~ |  | MM3Z3V6T1G
 |  | D401 | 3.6V | Device:D_Zener | Diode_SMD:D_SOD-323_HandSoldering | ~ |  | MM3Z3V6T1G
 |  | D402 | 3.6V | Device:D_Zener | Diode_SMD:D_SOD-323_HandSoldering | ~ |  | MM3Z3V6T1G
 |  | D403 | 3.6V | Device:D_Zener | Diode_SMD:D_SOD-323_HandSoldering | ~ |  | MM3Z3V6T1G
 |  | D404 | 3.6V | Device:D_Zener | Diode_SMD:D_SOD-323_HandSoldering | ~ |  | MM3Z3V6T1G
 |  | D405 | YELLOW | Device:LED | LED_SMD:LED_0603_1608Metric_Pad1.05x0.95mm_HandSolder | ~
 |  | D406 | YELLOW | Device:LED | LED_SMD:LED_0603_1608Metric_Pad1.05x0.95mm_HandSolder | ~
 |  | D407 | YELLOW | Device:LED | LED_SMD:LED_0603_1608Metric_Pad1.05x0.95mm_HandSolder | ~
 |  | D408 | YELLOW | Device:LED | LED_SMD:LED_0603_1608Metric_Pad1.05x0.95mm_HandSolder | ~
 |  | D409 | GREEN | Device:LED | LED_SMD:LED_0603_1608Metric_Pad1.05x0.95mm_HandSolder | ~
 |  | D410 | RED | Device:LED | LED_SMD:LED_0603_1608Metric_Pad1.05x0.95mm_HandSolder | ~
 |  | D411 | 3.6V | Device:D_Zener | Diode_SMD:D_SOD-323_HandSoldering | ~ |  | MM3Z3V6T1G
 |  | D412 | 3.6V | Device:D_Zener | Diode_SMD:D_SOD-323_HandSoldering | ~ |  | MM3Z3V6T1G
 |  | D413 | 3.6V | Device:D_Zener | Diode_SMD:D_SOD-323_HandSoldering | ~ |  | MM3Z3V6T1G
 |  | D501 | 150505M173300 | LED:SMLVN6RGB | LED_SMD:LED_RGB_5050-6 | https://www.rohm.com/datasheet/SMLVN6RGB1U |  |  | 150505M173300
 |  | D701 | DSS15UTR | Device:D | Diode_SMD:D_SOD-123F | ~
 |  | D702 | RED | Device:LED | LED_SMD:LED_0603_1608Metric_Pad1.05x0.95mm_HandSolder | ~
 |  | D703 | GREEN | Device:LED | LED_SMD:LED_0603_1608Metric_Pad1.05x0.95mm_HandSolder | ~
 |  | D801 | CDBC380-G | Device:D_Schottky | Diode_SMD:D_SMC_Handsoldering | ~
 |  | D901 | DSS15UTR | Device:D | Diode_SMD:D_SOD-123F | ~
 |  | D902 | DSS15UTR | Device:D | Diode_SMD:D_SOD-123F | ~
 |  | D903 | DSS15UTR | Device:D | Diode_SMD:D_SOD-123F | ~
 |  | D904 | DSS15UTR | Device:D | Diode_SMD:D_SOD-123F | ~
 |  | D905 | DSS15UTR | Device:D | Diode_SMD:D_SOD-123F | ~
 |  | D906 | DSS15UTR | Device:D | Diode_SMD:D_SOD-123F | ~
 |  | D907 | DSS15UTR | Device:D | Diode_SMD:D_SOD-123F | ~
 |  | D908 | DSS15UTR | Device:D | Diode_SMD:D_SOD-123F | ~
 |  | D1001 | DSS15UTR | Device:D | Diode_SMD:D_SOD-123F | ~
 |  | D1002 | DSS15UTR | Device:D | Diode_SMD:D_SOD-123F | ~
 |  | D1003 | DSS15UTR | Device:D | Diode_SMD:D_SOD-123F | ~
 |  | D1004 | DSS15UTR | Device:D | Diode_SMD:D_SOD-123F | ~
 |  | D1005 | DSS15UTR | Device:D | Diode_SMD:D_SOD-123F | ~
 |  | D1006 | DSS15UTR | Device:D | Diode_SMD:D_SOD-123F | ~
 |  | D1007 | DSS15UTR | Device:D | Diode_SMD:D_SOD-123F | ~
 |  | D1008 | DSS15UTR | Device:D | Diode_SMD:D_SOD-123F | ~
 |  | D1201 | 3.6V | Device:D_Zener | Diode_SMD:D_SOD-323_HandSoldering | ~ |  | MM3Z3V6T1G
 |  | D1202 | 3.6V | Device:D_Zener | Diode_SMD:D_SOD-323_HandSoldering | ~ |  | MM3Z3V6T1G
 |  | D1401 | DSS15UTR | Device:D | Diode_SMD:D_SOD-123F | ~
 |  | D1402 | DSS15UTR | Device:D | Diode_SMD:D_SOD-123F | ~
 |  | D1403 | DSS15UTR | Device:D | Diode_SMD:D_SOD-123F | ~
 |  | D1404 | DSS15UTR | Device:D | Diode_SMD:D_SOD-123F | ~
 |  | D1405 | DSS15UTR | Device:D | Diode_SMD:D_SOD-123F | ~
 |  | D1406 | DSS15UTR | Device:D | Diode_SMD:D_SOD-123F | ~
 |  | D1407 | DSS15UTR | Device:D | Diode_SMD:D_SOD-123F | ~
 |  | D1408 | DSS15UTR | Device:D | Diode_SMD:D_SOD-123F | ~
 |  | D1409 | DSS15UTR | Device:D | Diode_SMD:D_SOD-123F | ~
 |  | D1410 | DSS15UTR | Device:D | Diode_SMD:D_SOD-123F | ~
 |  | D1411 | DSS15UTR | Device:D | Diode_SMD:D_SOD-123F | ~
 |  | D1412 | DSS15UTR | Device:D | Diode_SMD:D_SOD-123F | ~
 |  | D1413 | DSS15UTR | Device:D | Diode_SMD:D_SOD-123F | ~
 |  | D1414 | DSS15UTR | Device:D | Diode_SMD:D_SOD-123F | ~
 |  | D1415 | DSS15UTR | Device:D | Diode_SMD:D_SOD-123F | ~
 |  | D1416 | DSS15UTR | Device:D | Diode_SMD:D_SOD-123F | ~
 |  | F1501 | 7.5A | Device:Fuse | Custom-Electromechanical:Keystone_3557 | ~
 |  | F1502 | 25A | Device:Fuse | Custom-Electromechanical:Keystone_3557 | ~
 |  | G101 | Quickstep Logo | Custom-Misc:Graphic_Placeholder | Custom-Graphics:qs_logo
 |  | H101 | M3 | Mechanical:MountingHole | MountingHole:MountingHole_3.2mm_M3_Pad | ~
 |  | H102 | M3 | Mechanical:MountingHole | MountingHole:MountingHole_3.2mm_M3_Pad | ~
 |  | H103 | M3 | Mechanical:MountingHole | MountingHole:MountingHole_3.2mm_M3_Pad | ~
 |  | H104 | M3 | Mechanical:MountingHole | MountingHole:MountingHole_3.2mm_M3_Pad | ~
 |  | H105 | M3 | Mechanical:MountingHole | MountingHole:MountingHole_3.2mm_M3_Pad | ~
 |  | H106 | M3 | Mechanical:MountingHole | MountingHole:MountingHole_3.2mm_M3_Pad | ~
 |  | H107 | M3 | Mechanical:MountingHole | MountingHole:MountingHole_3.2mm_M3_Pad | ~
 |  | H108 | M3 | Mechanical:MountingHole | MountingHole:MountingHole_3.2mm_M3_Pad | ~
 |  | H109 | M3 | Mechanical:MountingHole | MountingHole:MountingHole_3.2mm_M3_Pad | ~
 |  | H110 | M3 | Mechanical:MountingHole | MountingHole:MountingHole_3.2mm_M3_Pad | ~
 |  | H111 | M5 | Mechanical:MountingHole | MountingHole:MountingHole_5.3mm_M5_Pad
 |  | H112 | M5 | Mechanical:MountingHole | MountingHole:MountingHole_5.3mm_M5_Pad
 |  | H113 | M5 | Mechanical:MountingHole | MountingHole:MountingHole_5.3mm_M5_Pad
 |  | H114 | M5 | Mechanical:MountingHole | MountingHole:MountingHole_5.3mm_M5_Pad
 |  | H115 | M5 | Mechanical:MountingHole | MountingHole:MountingHole_5.3mm_M5_Pad
 |  | H116 | M5 | Mechanical:MountingHole | MountingHole:MountingHole_5.3mm_M5_Pad
 |  | J101 | Conn_01x04 | Connector_Generic:Conn_01x04 | Connector_JST:JST_XH_B4B-XH-A_1x04_P2.50mm_Vertical | ~
 |  | J201 | SD_Card | Connector:SD_Card | Custom-Electromechanical:SD_TE_2041021 | http://portal.fciconnect.com/Comergent//fci/drawing/10067847.pdf |  | 2041021-4
 |  | J601 | USB_A | Connector:USB_A | Daughterboards:USB_Adapter | ~
 |  | J602 | USB_B | Connector:USB_B | Custom-Electromechanical:CUI_UJ2-BH-W1-TH | ~ |  | USB-B1HSB6
 |  | J901 | Conn_02x03_Odd_Even | Connector_Generic:Conn_02x03_Odd_Even | Connector_IDC:IDC-Header_2x03_P2.54mm_Vertical | ~
 |  | J1001 | Conn_02x03_Odd_Even | Connector_Generic:Conn_02x03_Odd_Even | Connector_IDC:IDC-Header_2x03_P2.54mm_Vertical | ~
 |  | J1101 | Conn_02x13_Odd_Even | Connector_Generic:Conn_02x13_Odd_Even | Connector_IDC:IDC-Header_2x13_P2.54mm_Vertical | ~
 |  | J1201 | Conn_02x05_Odd_Even | Connector_Generic:Conn_02x05_Odd_Even | Connector_IDC:IDC-Header_2x05_P2.54mm_Vertical | ~
 |  | J1301 | Conn_02x03_Odd_Even | Connector_Generic:Conn_02x03_Odd_Even | Connector_IDC:IDC-Header_2x03_P2.54mm_Vertical | ~
 |  | J1401 | Conn_02x10_Odd_Even | Connector_Generic:Conn_02x10_Odd_Even | Connector_IDC:IDC-Header_2x10_P2.54mm_Vertical | ~
 |  | J1501 | Conn_01x02 | Connector_Generic:Conn_01x02 | Connector_JST:JST_XH_B2B-XH-A_1x02_P2.50mm_Vertical | ~
 |  | J1502 | Conn_01x04 | Connector_Generic:Conn_01x04 | Connector_JST:JST_XH_B4B-XH-A_1x04_P2.50mm_Vertical | ~
 |  | J1503 | Conn_XT | Custom-DiscreteSymbols:Conn_XT | Custom-Electromechanical:XT60-Male
 |  | L801 | 4.7uH | Device:L | Inductor_SMD:L_Bourns_SRR1260 | ~ |  | SRR1260-4R7Y
 |  | Q301 | AOD514 | Custom-DiscreteSymbols:AOD514 | Package_TO_SOT_SMD:TO-252-2 | http://www.vishay.com/docs/75129/sqj479ep.pdf
 |  | Q302 | AOD514 | Custom-DiscreteSymbols:AOD514 | Package_TO_SOT_SMD:TO-252-2 | http://www.vishay.com/docs/75129/sqj479ep.pdf
 |  | Q303 | NTR3C21NZT1G | Custom-DiscreteSymbols:NTR3C21NZT1G | Package_TO_SOT_SMD:SOT-23_Handsoldering | http://www.vishay.com/docs/75129/sqj479ep.pdf
 |  | Q304 | AOD514 | Custom-DiscreteSymbols:AOD514 | Package_TO_SOT_SMD:TO-252-2 | http://www.vishay.com/docs/75129/sqj479ep.pdf
 |  | Q401 | NTR3C21NZT1G | Custom-DiscreteSymbols:NTR3C21NZT1G | Package_TO_SOT_SMD:SOT-23_Handsoldering | http://www.vishay.com/docs/75129/sqj479ep.pdf
 |  | Q402 | NTR3C21NZT1G | Custom-DiscreteSymbols:NTR3C21NZT1G | Package_TO_SOT_SMD:SOT-23_Handsoldering | http://www.vishay.com/docs/75129/sqj479ep.pdf
 |  | Q501 | NTR3C21NZT1G | Custom-DiscreteSymbols:NTR3C21NZT1G | Package_TO_SOT_SMD:SOT-23_Handsoldering | http://www.vishay.com/docs/75129/sqj479ep.pdf
 |  | Q502 | NTR3C21NZT1G | Custom-DiscreteSymbols:NTR3C21NZT1G | Package_TO_SOT_SMD:SOT-23_Handsoldering | http://www.vishay.com/docs/75129/sqj479ep.pdf
 |  | Q503 | NTR3C21NZT1G | Custom-DiscreteSymbols:NTR3C21NZT1G | Package_TO_SOT_SMD:SOT-23_Handsoldering | http://www.vishay.com/docs/75129/sqj479ep.pdf
 |  | Q701 | NTR3C21NZT1G | Custom-DiscreteSymbols:NTR3C21NZT1G | Package_TO_SOT_SMD:SOT-23_Handsoldering | http://www.vishay.com/docs/75129/sqj479ep.pdf
 |  | Q801 | NTR3C21NZT1G | Custom-DiscreteSymbols:NTR3C21NZT1G | Package_TO_SOT_SMD:SOT-23_Handsoldering | http://www.vishay.com/docs/75129/sqj479ep.pdf
 |  | Q802 | AOD514 | Custom-DiscreteSymbols:AOD514 | Package_TO_SOT_SMD:TO-252-2 | http://www.vishay.com/docs/75129/sqj479ep.pdf
 |  | R201 | 1K | Device:R | Resistor_SMD:R_0603_1608Metric_Pad1.05x0.95mm_HandSolder | ~
 |  | R202 | 1K | Device:R | Resistor_SMD:R_0603_1608Metric_Pad1.05x0.95mm_HandSolder | ~
 |  | R203 | 10K | Device:R | Resistor_SMD:R_0603_1608Metric_Pad1.05x0.95mm_HandSolder | ~
 |  | R204 | 10K | Device:R | Resistor_SMD:R_0603_1608Metric_Pad1.05x0.95mm_HandSolder | ~
 |  | R205 | 10K | Device:R | Resistor_SMD:R_0603_1608Metric_Pad1.05x0.95mm_HandSolder | ~
 |  | R206 | 10K | Device:R | Resistor_SMD:R_0603_1608Metric_Pad1.05x0.95mm_HandSolder | ~
 |  | R207 | 10K | Device:R | Resistor_SMD:R_0603_1608Metric_Pad1.05x0.95mm_HandSolder | ~
 |  | R208 | 10K | Device:R | Resistor_SMD:R_0603_1608Metric_Pad1.05x0.95mm_HandSolder | ~
 |  | R209 | 10K | Device:R | Resistor_SMD:R_0603_1608Metric_Pad1.05x0.95mm_HandSolder | ~
 |  | R301 | 1K | Device:R | Resistor_SMD:R_0603_1608Metric_Pad1.05x0.95mm_HandSolder | ~
 |  | R302 | 1K | Device:R | Resistor_SMD:R_0603_1608Metric_Pad1.05x0.95mm_HandSolder | ~
 |  | R303 | 390 | Device:R | Resistor_SMD:R_0603_1608Metric_Pad1.05x0.95mm_HandSolder | ~
 |  | R304 | 390R | Device:R | Resistor_SMD:R_0603_1608Metric_Pad1.05x0.95mm_HandSolder | ~
 |  | R305 | 240K | Device:R | Resistor_SMD:R_0603_1608Metric_Pad1.05x0.95mm_HandSolder | ~
 |  | R306 | 390R | Device:R | Resistor_SMD:R_0603_1608Metric_Pad1.05x0.95mm_HandSolder | ~
 |  | R307 | 240K | Device:R | Resistor_SMD:R_0603_1608Metric_Pad1.05x0.95mm_HandSolder | ~
 |  | R308 | 240K | Device:R | Resistor_SMD:R_0603_1608Metric_Pad1.05x0.95mm_HandSolder | ~
 |  | R309 | 4K7 | Device:R | Resistor_SMD:R_0603_1608Metric_Pad1.05x0.95mm_HandSolder | ~
 |  | R310 | 4K7 | Device:R | Resistor_SMD:R_0603_1608Metric_Pad1.05x0.95mm_HandSolder | ~
 |  | R311 | 390 | Device:R | Resistor_SMD:R_0603_1608Metric_Pad1.05x0.95mm_HandSolder | ~
 |  | R312 | 390 | Device:R | Resistor_SMD:R_0603_1608Metric_Pad1.05x0.95mm_HandSolder | ~
 |  | R313 | 4K7 | Device:R | Resistor_SMD:R_0603_1608Metric_Pad1.05x0.95mm_HandSolder | ~
 |  | R314 | 4K7 | Device:R | Resistor_SMD:R_0603_1608Metric_Pad1.05x0.95mm_HandSolder | ~
 |  | R401 | 10K | Device:R | Resistor_SMD:R_0603_1608Metric_Pad1.05x0.95mm_HandSolder | ~
 |  | R402 | 10K | Device:R | Resistor_SMD:R_0603_1608Metric_Pad1.05x0.95mm_HandSolder | ~
 |  | R403 | 10K | Device:R | Resistor_SMD:R_0603_1608Metric_Pad1.05x0.95mm_HandSolder | ~
 |  | R404 | 10K | Device:R | Resistor_SMD:R_0603_1608Metric_Pad1.05x0.95mm_HandSolder | ~
 |  | R405 | 10K | Device:R | Resistor_SMD:R_0603_1608Metric_Pad1.05x0.95mm_HandSolder | ~
 |  | R406 | 10K | Device:R | Resistor_SMD:R_0603_1608Metric_Pad1.05x0.95mm_HandSolder | ~
 |  | R407 | 10K | Device:R | Resistor_SMD:R_0603_1608Metric_Pad1.05x0.95mm_HandSolder | ~
 |  | R408 | 10K | Device:R | Resistor_SMD:R_0603_1608Metric_Pad1.05x0.95mm_HandSolder | ~
 |  | R409 | 1K | Device:R | Resistor_SMD:R_0603_1608Metric_Pad1.05x0.95mm_HandSolder | ~
 |  | R410 | 1K | Device:R | Resistor_SMD:R_0603_1608Metric_Pad1.05x0.95mm_HandSolder | ~
 |  | R411 | 1K | Device:R | Resistor_SMD:R_0603_1608Metric_Pad1.05x0.95mm_HandSolder | ~
 |  | R412 | 1K | Device:R | Resistor_SMD:R_0603_1608Metric_Pad1.05x0.95mm_HandSolder | ~
 |  | R413 | 1K | Device:R | Resistor_SMD:R_0603_1608Metric_Pad1.05x0.95mm_HandSolder | ~
 |  | R414 | 10K | Device:R | Resistor_SMD:R_0603_1608Metric_Pad1.05x0.95mm_HandSolder | ~
 |  | R415 | 240K | Device:R | Resistor_SMD:R_0603_1608Metric_Pad1.05x0.95mm_HandSolder | ~
 |  | R416 | 240K | Device:R | Resistor_SMD:R_0603_1608Metric_Pad1.05x0.95mm_HandSolder | ~
 |  | R417 | 1K | Device:R | Resistor_SMD:R_0603_1608Metric_Pad1.05x0.95mm_HandSolder | ~
 |  | R418 | 1K | Device:R | Resistor_SMD:R_0603_1608Metric_Pad1.05x0.95mm_HandSolder | ~
 |  | R419 | 1K | Device:R | Resistor_SMD:R_0603_1608Metric_Pad1.05x0.95mm_HandSolder | ~
 |  | R420 | 1K | Device:R | Resistor_SMD:R_0603_1608Metric_Pad1.05x0.95mm_HandSolder | ~
 |  | R421 | 1K | Device:R | Resistor_SMD:R_0603_1608Metric_Pad1.05x0.95mm_HandSolder | ~
 |  | R501 | 4K7 | Device:R | Resistor_SMD:R_0603_1608Metric_Pad1.05x0.95mm_HandSolder | ~
 |  | R502 | 4K7 | Device:R | Resistor_SMD:R_0603_1608Metric_Pad1.05x0.95mm_HandSolder | ~
 |  | R503 | 240K | Device:R | Resistor_SMD:R_0603_1608Metric_Pad1.05x0.95mm_HandSolder | ~
 |  | R504 | 4K7 | Device:R | Resistor_SMD:R_0603_1608Metric_Pad1.05x0.95mm_HandSolder | ~
 |  | R505 | 4K7 | Device:R | Resistor_SMD:R_0603_1608Metric_Pad1.05x0.95mm_HandSolder | ~
 |  | R506 | 390 | Device:R | Resistor_SMD:R_0603_1608Metric_Pad1.05x0.95mm_HandSolder | ~
 |  | R507 | 390 | Device:R | Resistor_SMD:R_0603_1608Metric_Pad1.05x0.95mm_HandSolder | ~
 |  | R508 | 390 | Device:R | Resistor_SMD:R_0603_1608Metric_Pad1.05x0.95mm_HandSolder | ~
 |  | R509 | 390 | Device:R | Resistor_SMD:R_0603_1608Metric_Pad1.05x0.95mm_HandSolder | ~
 |  | R510 | 390 | Device:R | Resistor_SMD:R_0603_1608Metric_Pad1.05x0.95mm_HandSolder | ~
 |  | R511 | 240K | Device:R | Resistor_SMD:R_0603_1608Metric_Pad1.05x0.95mm_HandSolder | ~
 |  | R512 | 240K | Device:R | Resistor_SMD:R_0603_1608Metric_Pad1.05x0.95mm_HandSolder | ~
 |  | R513 | 240K | Device:R | Resistor_SMD:R_0603_1608Metric_Pad1.05x0.95mm_HandSolder | ~
 |  | R514 | 1K | Device:R | Resistor_SMD:R_0603_1608Metric_Pad1.05x0.95mm_HandSolder | ~
 |  | R515 | 1K | Device:R | Resistor_SMD:R_0603_1608Metric_Pad1.05x0.95mm_HandSolder | ~
 |  | R516 | 1K | Device:R | Resistor_SMD:R_0603_1608Metric_Pad1.05x0.95mm_HandSolder | ~
 |  | R701 | 10K | Device:R | Resistor_SMD:R_0603_1608Metric_Pad1.05x0.95mm_HandSolder | ~
 |  | R702 | 10K | Device:R | Resistor_SMD:R_0603_1608Metric_Pad1.05x0.95mm_HandSolder | ~
 |  | R703 | 10K | Device:R | Resistor_SMD:R_0603_1608Metric_Pad1.05x0.95mm_HandSolder | ~
 |  | R704 | 10K | Device:R | Resistor_SMD:R_0603_1608Metric_Pad1.05x0.95mm_HandSolder | ~
 |  | R705 | 10K | Device:R | Resistor_SMD:R_0603_1608Metric_Pad1.05x0.95mm_HandSolder | ~
 |  | R706 | 10K | Device:R | Resistor_SMD:R_0603_1608Metric_Pad1.05x0.95mm_HandSolder | ~
 |  | R707 | 10K | Device:R | Resistor_SMD:R_0603_1608Metric_Pad1.05x0.95mm_HandSolder | ~
 |  | R708 | 10K | Device:R | Resistor_SMD:R_0603_1608Metric_Pad1.05x0.95mm_HandSolder | ~
 |  | R709 | 390 | Device:R | Resistor_SMD:R_0603_1608Metric_Pad1.05x0.95mm_HandSolder | ~
 |  | R710 | 10K | Device:R | Resistor_SMD:R_0603_1608Metric_Pad1.05x0.95mm_HandSolder | ~
 |  | R711 | 390 | Device:R | Resistor_SMD:R_0603_1608Metric_Pad1.05x0.95mm_HandSolder | ~
 |  | R712 | 1K | Device:R | Resistor_SMD:R_0603_1608Metric_Pad1.05x0.95mm_HandSolder | ~
 |  | R713 | 10K | Device:R | Resistor_SMD:R_0603_1608Metric_Pad1.05x0.95mm_HandSolder | ~
 |  | R714 | 10K | Device:R | Resistor_SMD:R_0603_1608Metric_Pad1.05x0.95mm_HandSolder | ~
 |  | R715 | 1K | Device:R | Resistor_SMD:R_0603_1608Metric_Pad1.05x0.95mm_HandSolder | ~
 |  | R801 | 16.9K | Device:R | Resistor_SMD:R_0603_1608Metric_Pad1.05x0.95mm_HandSolder | ~
 |  | R802 | 4.7K | Device:R | Resistor_SMD:R_0603_1608Metric_Pad1.05x0.95mm_HandSolder | ~
 |  | R803 | 1K | Device:R | Resistor_SMD:R_0603_1608Metric_Pad1.05x0.95mm_HandSolder | ~
 |  | R804 | 10K | Device:R | Resistor_SMD:R_0603_1608Metric_Pad1.05x0.95mm_HandSolder | ~
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

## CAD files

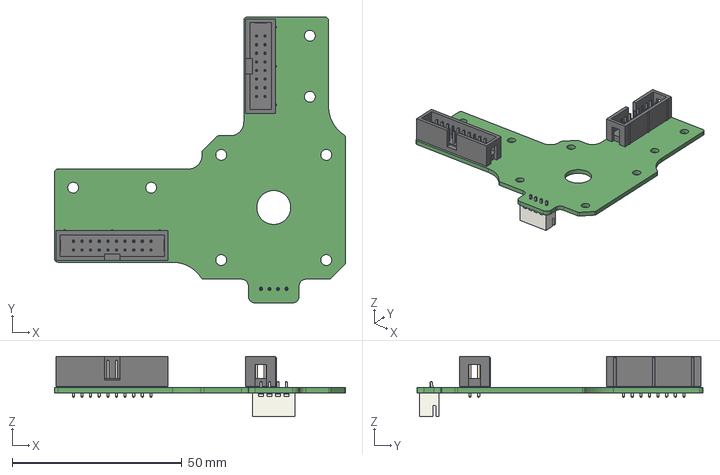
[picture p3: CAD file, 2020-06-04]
adapter_boards/gantry_x_motor_breakout/gantry_x_motor_breakout.step
85.8 x 84.3 x 17.8 mm

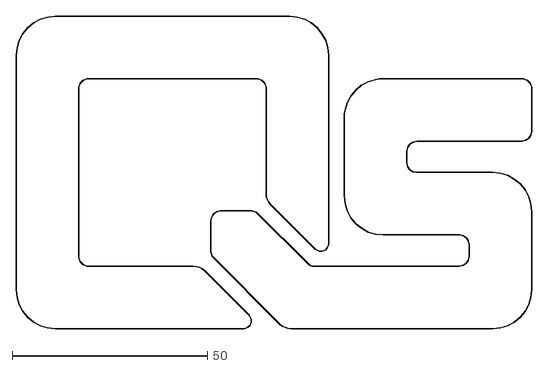
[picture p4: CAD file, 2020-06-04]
quickstep_controller/Quickstep_Logo.dxf
132.0 x 80.0

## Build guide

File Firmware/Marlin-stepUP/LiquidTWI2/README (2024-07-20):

LiquidTWI2
==========

A lean, high speed I2C LCD Library for Arduino, which supports MCP23008 (Adafruit LCD Backpack) and MCP23017 (Adafruit RGB LCD Shield)

hacked by Sam C. Lin / http://www.lincomatic.com
from 
  LiquidTWI by Matt Falcon (FalconFour) / http://falconfour.com
  logic gleaned from Adafruit RGB LCD Shield library
  Panelolu2 support by Tony Lock / http://blog.think3dprint3d.com
  Panelolu2 integration by Robert F-C / https://github.com/buildrob
  enhancements by Nick Sayer / https://github.com/nsayer

Compatible with Adafruit I2C LCD backpack (MCP23008) and
Adafruit RGB LCD Shield (and optionally, Panelolu2)

For more information see 
 http://blog.lincomatic.com/?tag=LiquidTWI2
 http://forums.adafruit.com/viewtopic.php?f=19&t=21586
 Panelolu2 usage see
 http://blog.think3dprint3d.com/2012/12/mcp23017-i2c.html

  Version 1.2.7

  Changelog:

  * 1.2.7 / 20190624 SCL
  fixed row offset issue w/ 16x4 LCD per https://github.com/lincomatic/LiquidTWI2/issues/15

  * 1.2.6 / 20140220 SCL
  added device detected guard to home() & buzz()

  * 1.2.5 / 20130725 SCL
  added LcdDetected() from Scott Rubin

  * 1.2.4 / 20130409 SCL
  buzz() fixes from buildrob

  * 1.2.3 / 20130322 SCL
  PANELOLU2 support cleanup and always enabled when MCP23017 by buildrob
  buzz() now works for Panucatt Viki as well

  * 1.2.2 / 20130120 SCL
  make setMCPType() a no-op when only one MCPxxxx defined instead
  of removing it

  * 1.2.1 / 20130102 SCL
  disable PANELOLU2 by default

  * 1.2.0 / 20130101 SCL
  added DETECT_DEVICE

  * 1.1.1 / 20121219 SCL
  added Tony Lock's Panelolu2 enhancements

  * 1.1.0 / 20121018 SCL
  use 8-bit GPIO for writing on MCP23017 for 25% speed increase
  with only 14 byte size increase

  * 1.0.0 / 20121016 SCL
  initial release

  Distributed with as free-will a license as is available given this code's long
  associative chain of licenses (LiquidCrystal -> Arduino -> Wiring -> ...?). Use
  it in any way you feel fit, profit or free, provided it fits in the licenses of
  its associated works.

  Installation:
  extract LiquidTWI2/ into <arduinosketchbook>/libraries/LiquidTWI2

  To use with Panelolu2
	lcd.setMCPType(LTI_TYPE_MCP23017);
    Panelolu2 only has encoder.. use PANELOLU_ENCODER_X bits instead of BUTTON_xxx

  Usage:
  Compatible with Arduino LiquidCrystal library except that setMCPType() MUST
  be called at least once before begin() is called

  // MCP23008 (Adafruit LCD Backpack)
  #include <Wire.h>
  #include <LiquidTWI2.h>
  LiquidTWI2 lcd(0x20);
  void setup() {
   lcd.setMCPType(LTI_TYPE_MCP23008); // must be called before begin()
   lcd.begin(16,2);
   lcd.setBacklight(HIGH); // only supports HIGH or LOW
  }
  void loop() {
   lcd.print("Hello World!");
   delay(500);
   lcd.clear();
   delay(500);
  }

  // MCP23017 (Adafruit RGB LCD Shield)
  #include <Wire.h>
  #include <LiquidTWI2.h>
  LiquidTWI2 lcd(0x20);
  void setup() {
   lcd.setMCPType(LTI_TYPE_MCP23017); // must be called before begin()
   lcd.begin(16,2);
   lcd.setBacklight(WHITE); // see LiquidTWI2.h for color options
  }
  void loop() {
   lcd.print("Hello World!");
   delay(500);
   lcd.clear();
   delay(500);
   uint8_t btns = lcd.readButtons();
  }

  If you change the i2c address of the board, set "lcd(0x20)" to your new 3-bit
  address.
  If you have more than a 16x2 LCD, change "lcd.begin(16,2)" to reflect the
  columns and rows of your LCD.

  Normally, the code will hang if the device is not detected at the specified
  i2c address.  If you want to compile your code for an optionally installed
  LCD, call the constructor with 2nd parameter deviceDetect=1. E.g:
     LiquidTWI2 lcd(0x20,1);
  When enabled, if the device is not detected at the specified address when
  begin() is called, then the rest of the function calls become NOOPs

  Note that the library can switch modes at runtime. Simply call setMCPType(),
  followed by begin().
  This allows you to create a firmware which is compatible with either kind
  of LCD module, and select the type from EEPROM.

  For memory-constrained projects, disable the unnecessary support by
  commenting out the corresponding MCP230xx in LiquidTWI2.h, and DETECT_DEVICE

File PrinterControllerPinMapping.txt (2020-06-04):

3D Printer Controller Pin Mapping

//============== MOTOR PINS =============
X_STEP - 22
X_DIR - 23
X_EN - 24
X_CS - 25
X_DIAG_0 - 26
X_DIAG_1 - 27

Y_STEP - 28
Y-DIR - 29
Y_EN - 30
Y-CS - 31
Y_DIAG_0 - 32
Y_DIAG_1 - 33

Z_STEP - 34
Z_DIR - 35
Z_EN - 36
Z_CS - 37
Z_DIAG_0 - 38
Z_DIAG_1 - 39

E_STEP - 40
E_DIR - 41
E_EN - 42
E_CS - 43
E_DIAG_0 - 44
E_DIAG_1 - 45

//============== LIMIT SWITCH ==============
X_MAX - 46
Y_MIN - 47
Z_MAX - 48
FIL_SEN - 49

//=============== TEMP CONTROL ================
EXT_THERM - A0
BED_THERM - A1

EXT_HEATER - 7
BED_HEATER - 9

PRINT_COOLING_FAN - 8

//===================== SD/SPI PINS ======================
/*
 * all stepper drivers and SD Card will be on the SPI bus
 * these need to be confirmed
 * all the SPI lines from the ICSP header
 */

SD_MOSI - 51
SD_MISO - 50
SD_SCK - 52
SD_CS - 17 
SD_CD - 16

//================= I2C_BUS (reserved) =================
//eeprom (24LC256 or similar, b1010000) and LCD panel will be on the I2C bus
SDA_PIN - 20 (but route from SDA pin)
SCL_PIN - 21 (but route from SCL pin)

//================ UART pins (reserved) ================
Serial1_TX - 1
Serial1_RX - 0

Serial2_TX - 18	//connect to ESP32 Rx
Serial2_RX - 19	//connect to ESP32 Tx

//================= LCD CONTROLLER PINS ================
ENCODER_A - 15
ENCODER_B - 14
ENCODER_CLICK  - -1

//===================== MISC_PINS ======================
PS_ON - 2
LED_PIN - 13 //diag

LED_RED - 10
LED_GREEN - 11
LED_BLUE - 12

//====================================################### ESP-32 PINS ###################======================================
//========== SD INTERFACE (Slot 1) ==========
// pull up all these lines with 10K
D0 - 7
D1 - 8
D2 - 9
D3 - 10
CMD - 11
CLK - 6

SERIAL_2_TX - 17 (wire to RX on arduino)
SERIAL_2_RX - 16 (wire to TX on arduino)

//for the SD card multiplexing
CD - 0
SD_SELECT - 2

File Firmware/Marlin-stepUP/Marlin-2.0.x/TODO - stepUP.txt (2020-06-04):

========== for custom LCD LEDs =============
 in ultralcd_HD44780.h lines 63-65:
X	- change LED_A/B/C to appropriate masks corresponding to
	  controller pin masks
 in ultralcd_HD44780.cpp lines 1076-1121:
X	- change all the LED turn-on conditionals to things I care about
X		- thermalManager.degBed and thermalManager.degHotend(0)
X		- card.isMounted()
X		- X_ENABLE_ON, Y_ENABLE_ON, Z_ENABLE_ON, E_ENABLE_ON (might have to include a header)

========== for automatic power control ===========
X - when drivers are enabled (CHECK HOMING AND G0/G1) 
X - when extruder temp is set 
X - when bed temp is set 

===== LCD INTERFACE ====
X - fix status LEDs
X - fix bug with MEDIA RELEASED button
X - fix switch POWER OFF button
X - possibly fix double click issue (watch how BUTTON_CLICKED works, esp with slow buttons!)

===== MISC ====
X - reupload with fixed y-dimension and fil sensor polarity
X - Add "Cold pull" in filament change menu (automated heat, extrusion, cooling to 100C

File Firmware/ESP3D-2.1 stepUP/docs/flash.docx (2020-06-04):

Flash instructions

From Sources:

A – Download git sources

B – copy content of git libraries directory to Arduino libraries directory (IniFile, AsyncWeb Server, SdFat)

C – Compile with ESP8266 CPU 160Mz and 4M/3MSPIFFS

D – Flash ESP

From Binaries:
1 – Without SD Card
A – Using esptool from ESP Arduino tools
https://github.com/igrr/esptool-ck/releases/download/0.4.5/

esptool.exe -vv -cd ck -cb 115200 -cp COM46 -ca 0x00000 -cf <full path to>espfw.bin

esptool.exe -vv -cd ck -cb 115200 -cp COM46 -ca 0x00100000 -cf <full path to>espfs.bin

B - Using esptool from espressif
https://github.com/espressif/esptool

2 – With SD Card

A -Firmware

Just put firmware espfw.bin on SD Card and reset/power board, if flash is successful it will be renamed espfw.ok, if not it will be renamed espfw.bad

B – SPIFFS

Just put file system image espfs.bin on SD Card and reset/power board, if flash is successful it will be renamed espfs.ok, if not it will be renamed espfs.bad

C – Configuration file

Just put file wconfig.txt on SD Card and reset/power board, if configuration is successful it will be renamed wconfig.ok, if not it will be renamed wconfig.bad

Note: if any .ok or .bad file already exists – it will be renamed first with a number like .ok1 – so .ok or .bad is always the latest one created

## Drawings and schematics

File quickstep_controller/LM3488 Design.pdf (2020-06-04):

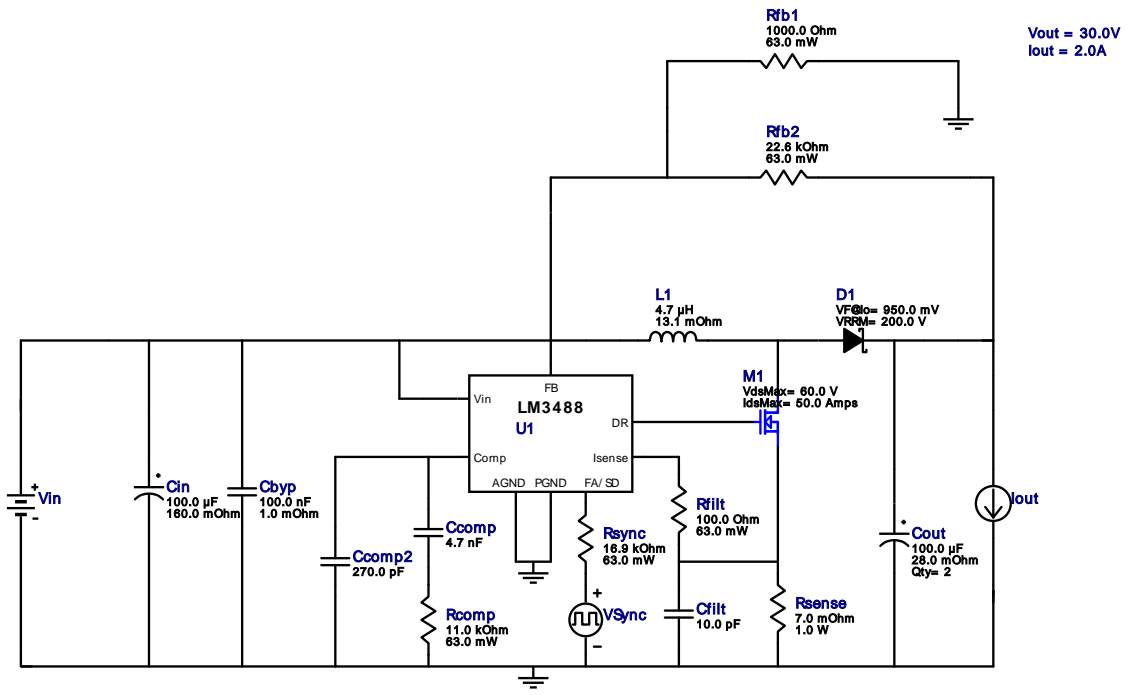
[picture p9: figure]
Cbyp 100.0 nF 1.0 mOhm; Cin 100.0 µF 160.0 mOhm; Cout 100.0 µF 28.0 mOhm Qty= 2; Cfilt 10.0 pF; M1 VdsMax= 60.0 V IdsMax= 50.0 Amps; Rfilt 100.0 Ohm 63.0 mW; Vout = 30.0V Iout = 2.0A; VSync; Rsense; 7.0 mOhm 1.0 W; Ccomp 4.7 nF Ccomp2; D1 VF@Io= 950.0 mV VRRM= 200.0 V; L1 4.7 µH 13.1 mOhm; Rsync 16.9 kOhm 63.0 mW; Rcomp 11.0 kOhm 63.0 mW; PGND; Vin; Comp; AGND; Isense; Rfb1 1000.0 Ohm 63.0 mW; Rfb2 22.6 kOhm 63.0 mW; Iout

Copyright © 2020, Texas Instruments Incorporated | 1 | ti.com/webench

WEBENCH®
Design Report LM3488MMX/NOPB : LM3488MMX/NOPB 10V-14V to 30.00V @ 2A February 2, 2020 18:08:21 GMT-08:00

## WEBENCH ® Design Report

Design : 13 LM3488MMX/NOPB
LM3488MMX/NOPB 10V-14V to 30.00V @ 2A

VinMin = 10.0V
VinMax = 14.0V
Vout = 30.0V
Iout = 2.0A

Device = LM3488MMX/NOPB
Topology = Boost
Created = 2020-02-01 09:10:06.972 BOM Cost = $4.64
BOM Count = 17
Total Pd = 4.6W
1. With the low turn of voltage of the LM34x8 your power supply may current limit before you reach your working input voltage. If this happens, or to preempt this from happening, you can include a low pass RC filter from input voltage to Vin on the IC. Make sure the rise time on the RC network is slower than your supply's rise time. If you are not using the syncronization feature of the part use the LM3478.

## Electrical BOM

Name | Manufacturer | Part Number | Properties | Qty Price | Footprint
Cbyp | MuRata | GRM155R71C104KA88D (http://search.murata.co.jp/Ceramy/PnsearchViewAction.do) Series= X7R | Cap= 100.0 nF ESR= 1.0 mOhm VDC= 16.0 V IRMS= 0.0 A
1 | $0.01
| | | | | 0402 3 mm²
Ccomp | TDK | CGA4C2C0G1H472J060AA (http://product.tdk.com/capacitor/mlcc/en/documents/mlcc%5Fautomotive%5Fgeneral%5Fen.pdf) Series= C0G/NP0

Cap= 4.7 nF
VDC= 50.0 V
IRMS= 0.0 A

1 $0.04
0805 7 mm²
Ccomp2 | Taiyo Yuden | UMK105CG271JV-F (http://media.digikey.com/pdf/Data%20Sheets/Taiyo%20Yuden%20PDFs%20URL%20links/Standard%20Multilayer%20Ceramic%20Caps.pdf) Series= C0G/NP0

Cap= 270.0 pF
VDC= 50.0 V
IRMS= 0.0 A

1 $0.01
0402 3 mm²
Cfilt | Samsung Electro- Mechanics | CL21C100JBANNNC (http://www.samsungsem.com/servlet/FileDownload?type%3Dspec%26file%3DCL21C100JBANNNC.pdf) Series= C0G/NP0

Cap= 10.0 pF
VDC= 50.0 V
IRMS= 0.0 A

1 $0.01
0805 7 mm²
Cin | Panasonic | EEE-FK1V101P (http://www.panasonic.com/industrial/components/pdf/smt%5Faec%5F050505.pdf) Series= FK

Cap= 100.0 uF
ESR= 160.0 mOhm
VDC= 35.0 V
IRMS= 600.0 mA

1 $0.21

SM_RADIAL_F 124 mm²

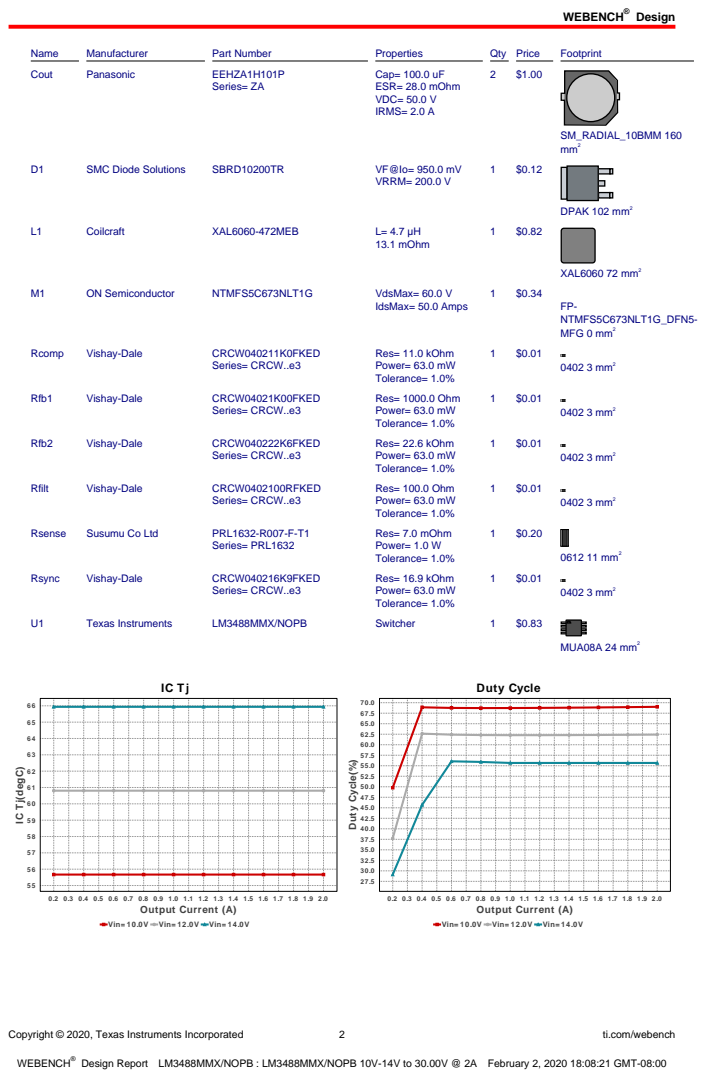
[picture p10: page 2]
Design; Copyright © 2020, Texas Instruments Incorporated; ti.com/webench; Name; Manufacturer; Part Number; Properties; Qty Price; Footprint; Cout; Panasonic; EEHZA1H101P; Series= ZA; Cap= 100.0 uF ESR= 28.0 mOhm VDC= 50.0 V IRMS= 2.0 A; SM_RADIAL_10BMM 160 mm²; SMC Diode Solutions; SBRD10200TR; VRRM= 200.0 V; DPAK 102 mm²; Coilcraft; XAL6060-472MEB; 13.1 mOhm; XAL6060 72 mm²; ON Semiconductor; NTMFS5C673NLT1G; VdsMax= 60.0 V; IdsMax= 50.0 Amps; FP- NTMFS5C673NLT1G_DFN5- MFG 0 mm²; Rcomp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

IC Tj(degC)

Vin= 10.0V Vin= 12.0V Vin= 14.0V

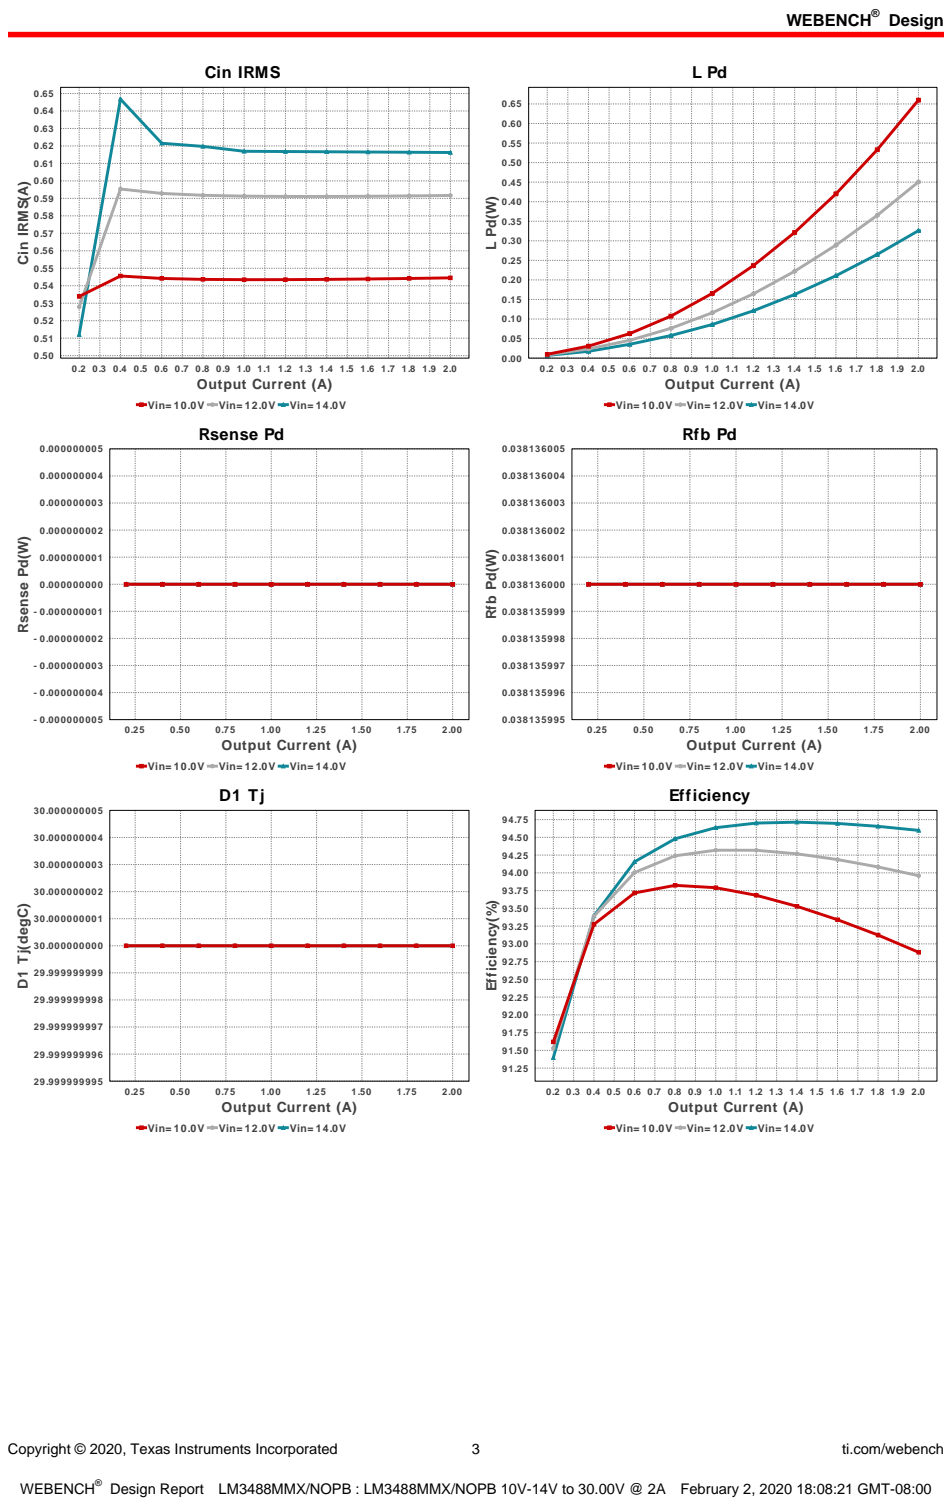
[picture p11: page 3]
Copyright © 2020, Texas Instruments Incorporated; ti.com/webench; Cin IRMS; 0.2 0.3 0.4 0.5 0.6 0.7 0.8 0.9 1.0 1.1 1.2 1.3 1.4 1.5 1.6 1.7 1.8 1.9 2.0 Output Current (A); Cin IRMS(A); 2.00 Output Current (A); Rsense Pd(W); Rfb Pd; Rfb Pd(W); D1 Tj(degC); Efficiency(%)

Vin= 10.0V Vin= 12.0V Vin= 14.0V
Rsense Pd

Efficiency

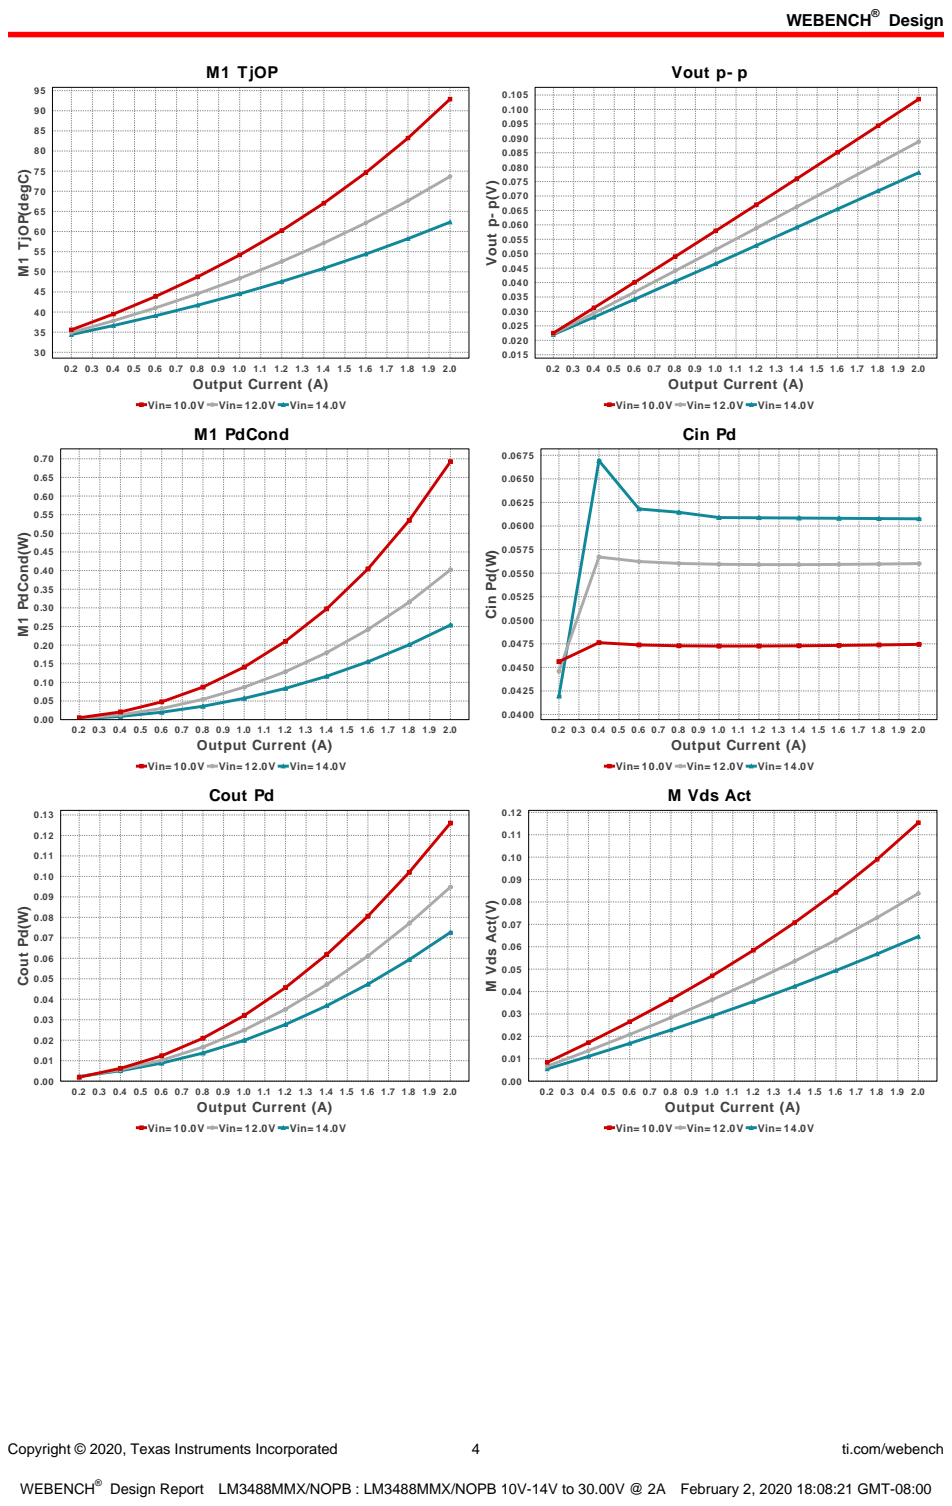
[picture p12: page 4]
Copyright © 2020, Texas Instruments Incorporated; ti.com/webench; M1 TjOP; 0.2 0.3 0.4 0.5 0.6 0.7 0.8 0.9 1.0 1.1 1.2 1.3 1.4 1.5 1.6 1.7 1.8 1.9 2.0 Output Current (A); M1 TjOP(degC); Vout p- p; Vout p- p(V); M1 PdCond(W); Cin Pd; Cin Pd(W); Cout Pd; Cout Pd(W); M Vds Act(V)

Vin= 10.0V Vin= 12.0V Vin= 14.0V
M1 PdCond

M Vds Act

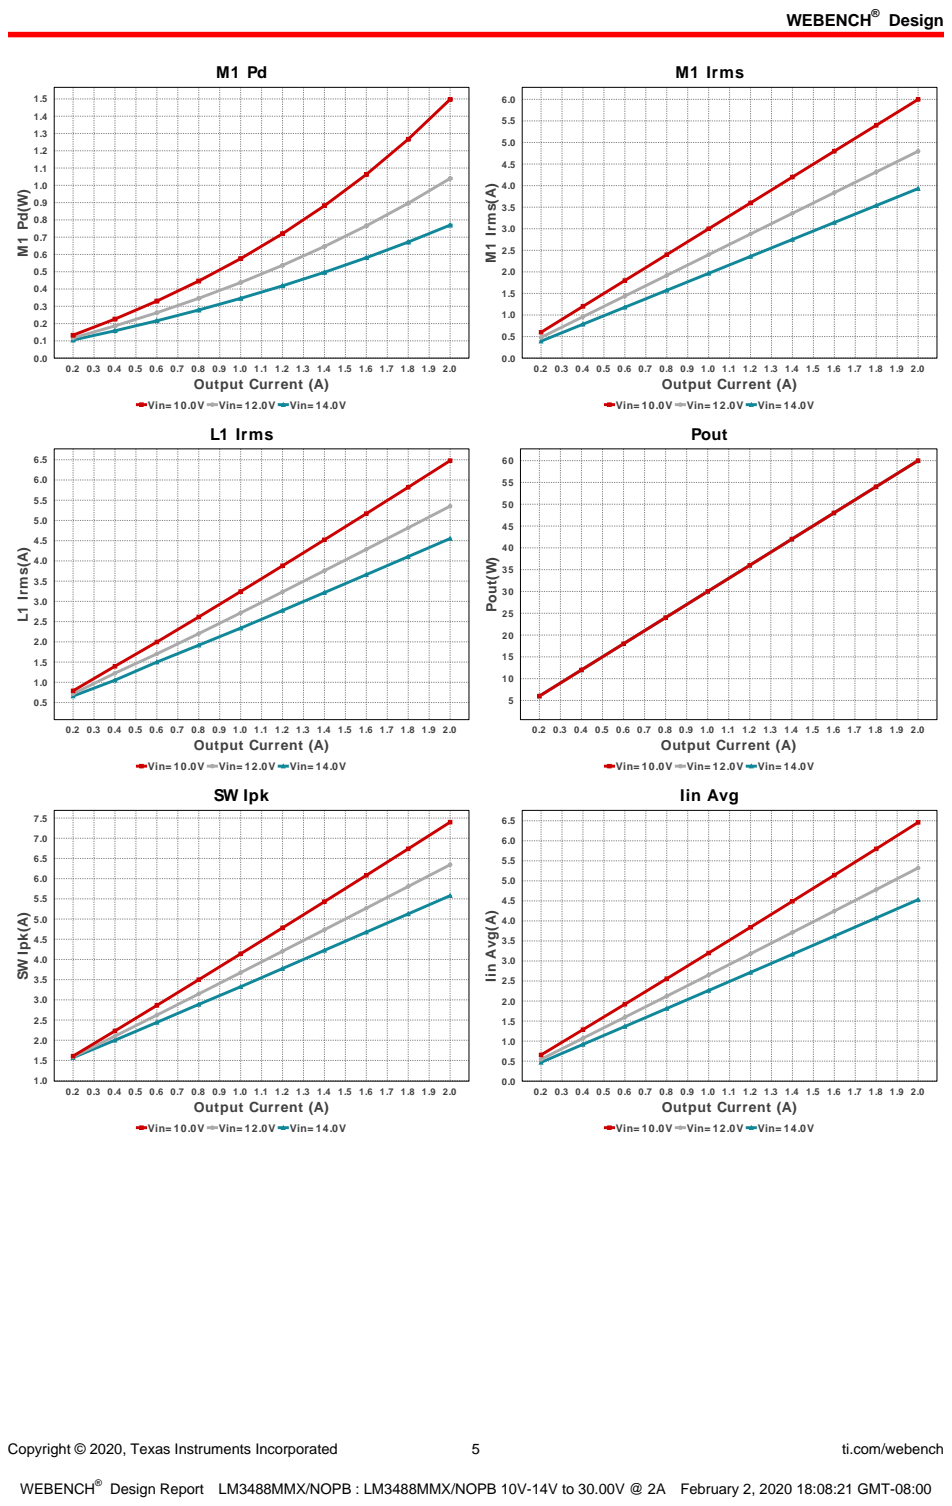
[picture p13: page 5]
Copyright © 2020, Texas Instruments Incorporated; ti.com/webench; 0.2 0.3 0.4 0.5 0.6 0.7 0.8 0.9 1.0 1.1 1.2 1.3 1.4 1.5 1.6 1.7 1.8 1.9 2.0 Output Current (A); M1 Irms; M1 Irms(A); L1 Irms; L1 Irms(A); Pout; Pout(W); SW Ipk; SW Ipk(A); Iin Avg; Iin Avg(A)

Vin= 10.0V Vin= 12.0V Vin= 14.0V

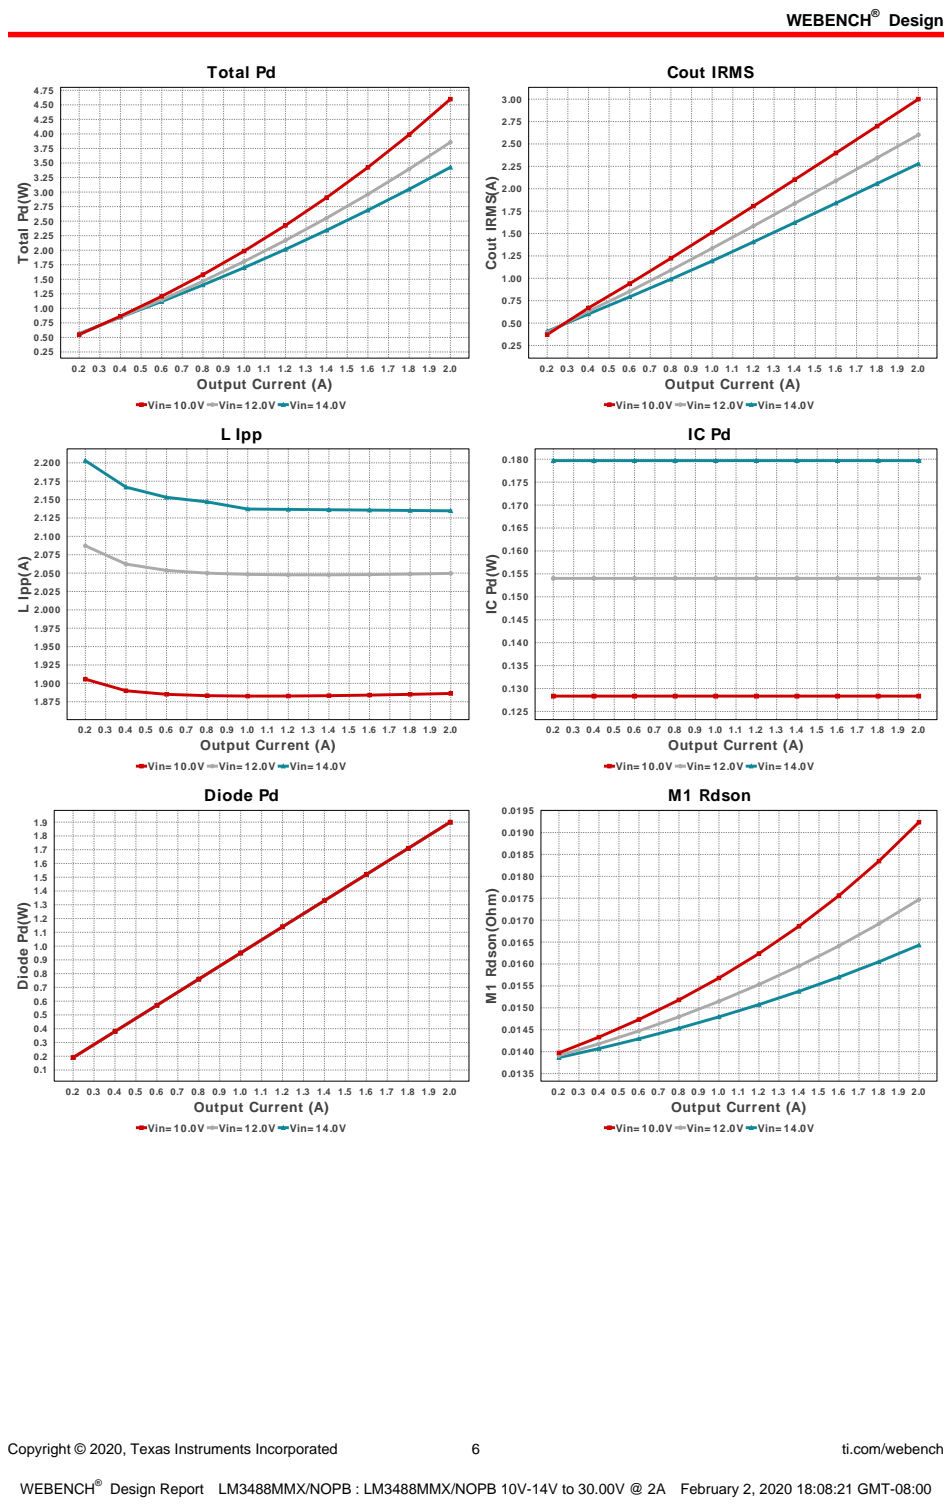
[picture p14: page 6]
Copyright © 2020, Texas Instruments Incorporated; ti.com/webench; Total Pd; 0.2 0.3 0.4 0.5 0.6 0.7 0.8 0.9 1.0 1.1 1.2 1.3 1.4 1.5 1.6 1.7 1.8 1.9 2.0 Output Current (A); Total Pd(W); Cout IRMS; Cout IRMS(A); L Ipp; L Ipp(A); Diode Pd(W); M1 Rdson(Ohm)

Vin= 10.0V Vin= 12.0V Vin= 14.0V

Diode Pd

M1 Rdson
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

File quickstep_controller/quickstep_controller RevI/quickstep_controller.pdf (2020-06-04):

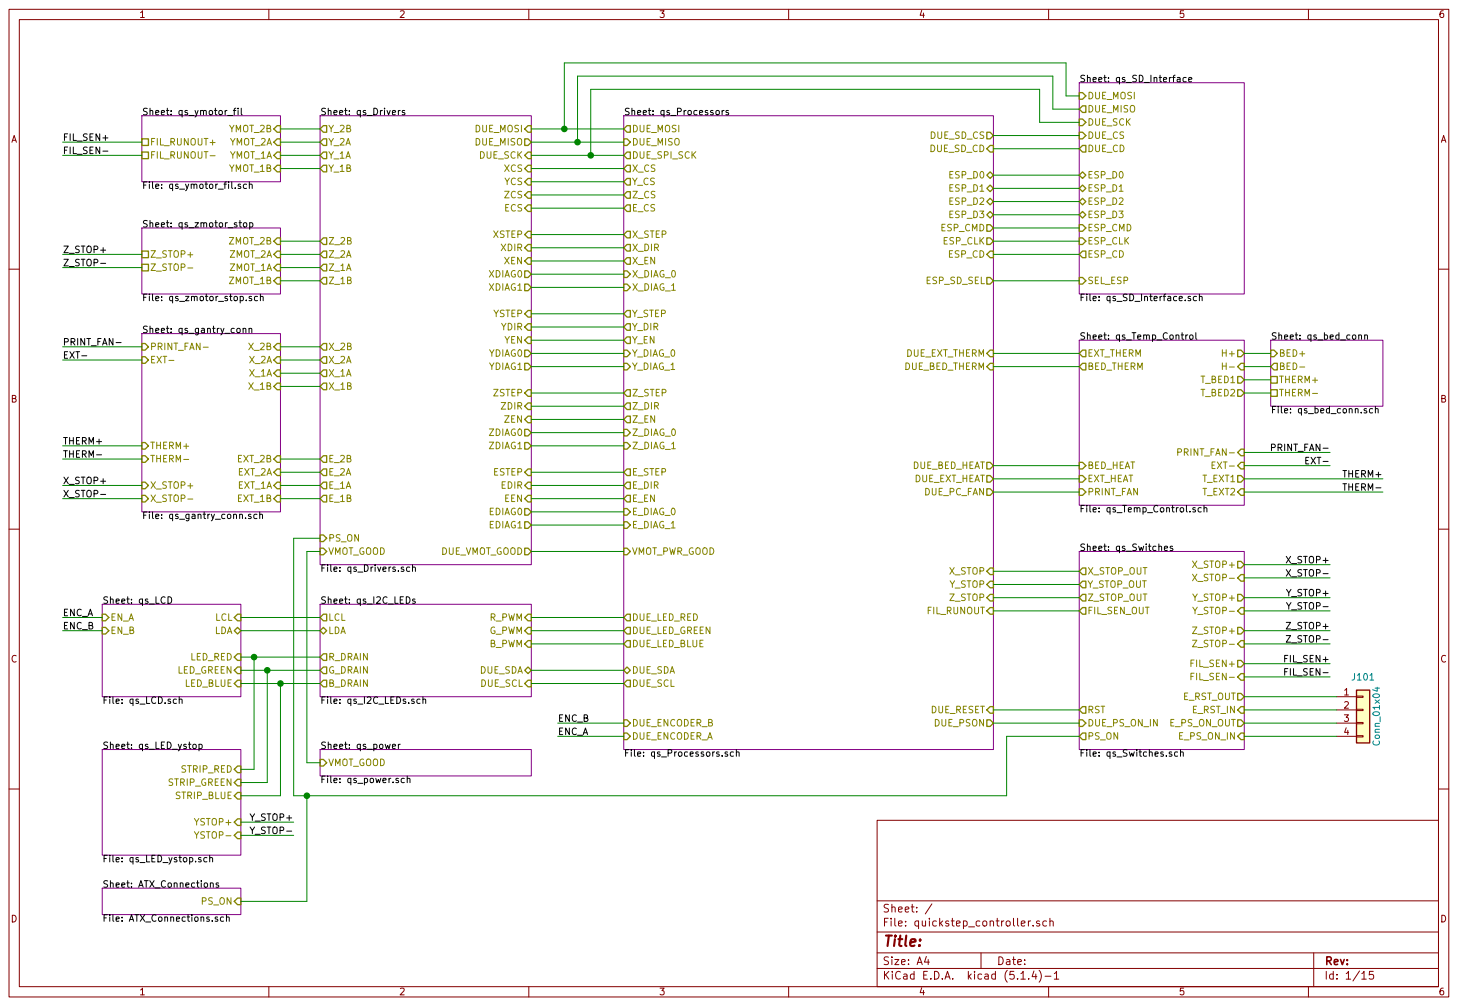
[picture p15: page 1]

File: qs_bed_conn.sch BED- BED+ THERM+ THERM- Sheet: qs_LCD

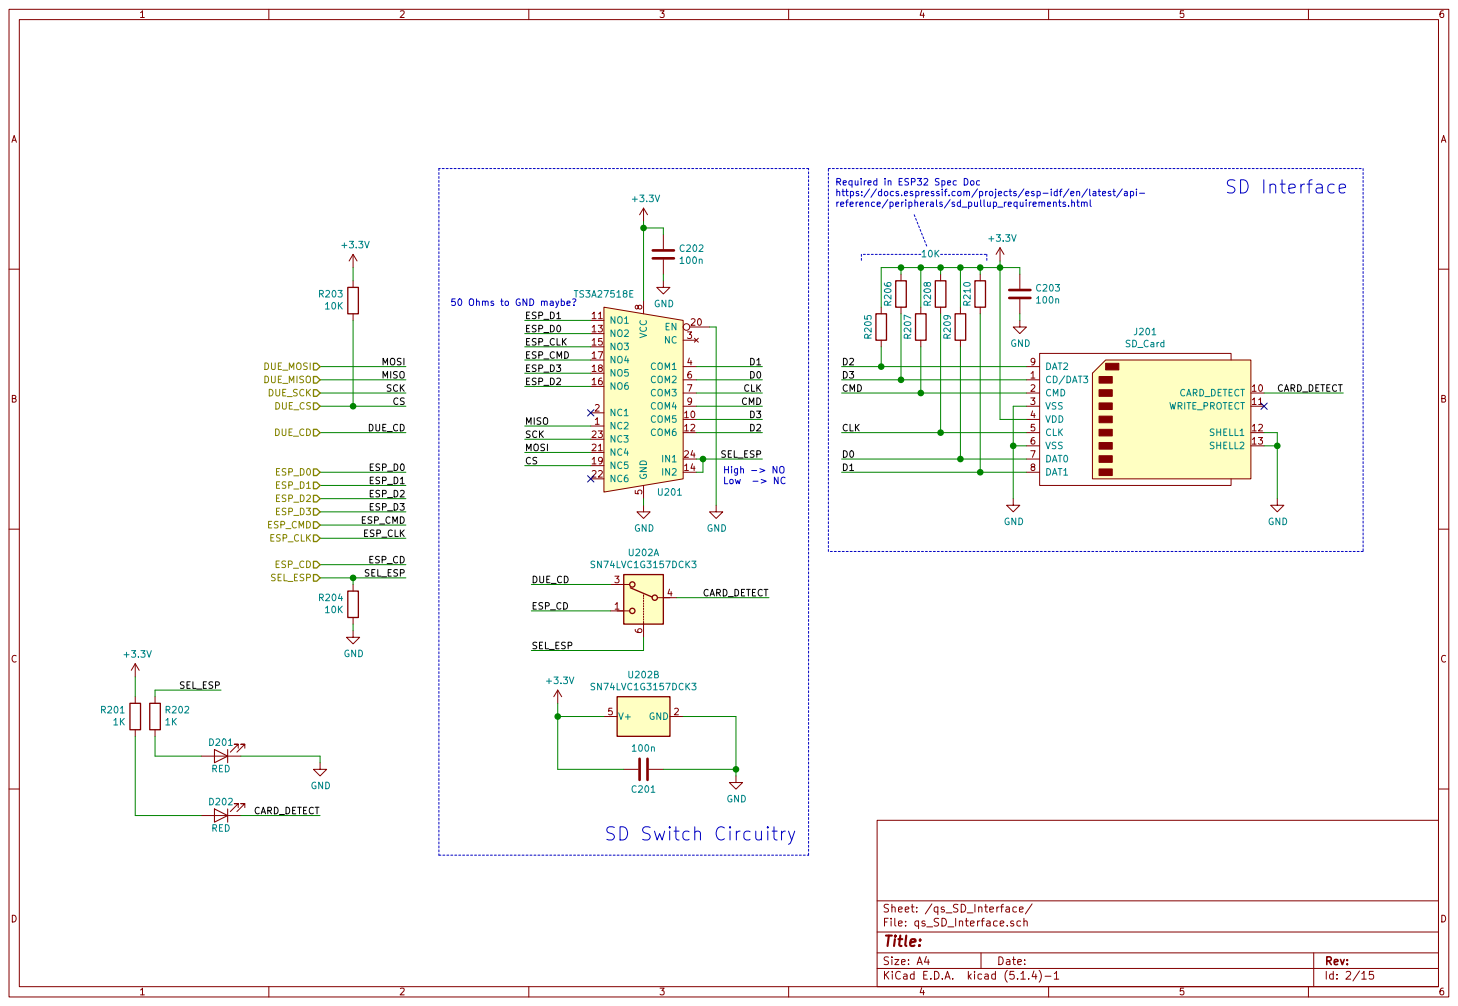
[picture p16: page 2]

Required in ESP32 Spec Doc
https://docs.espressif.com/projects/esp-idf/en/latest/api-
reference/peripherals/sd_pullup_requirements.html
Low -> NC SD Switch Circuitry

50 Ohms to GND maybe?

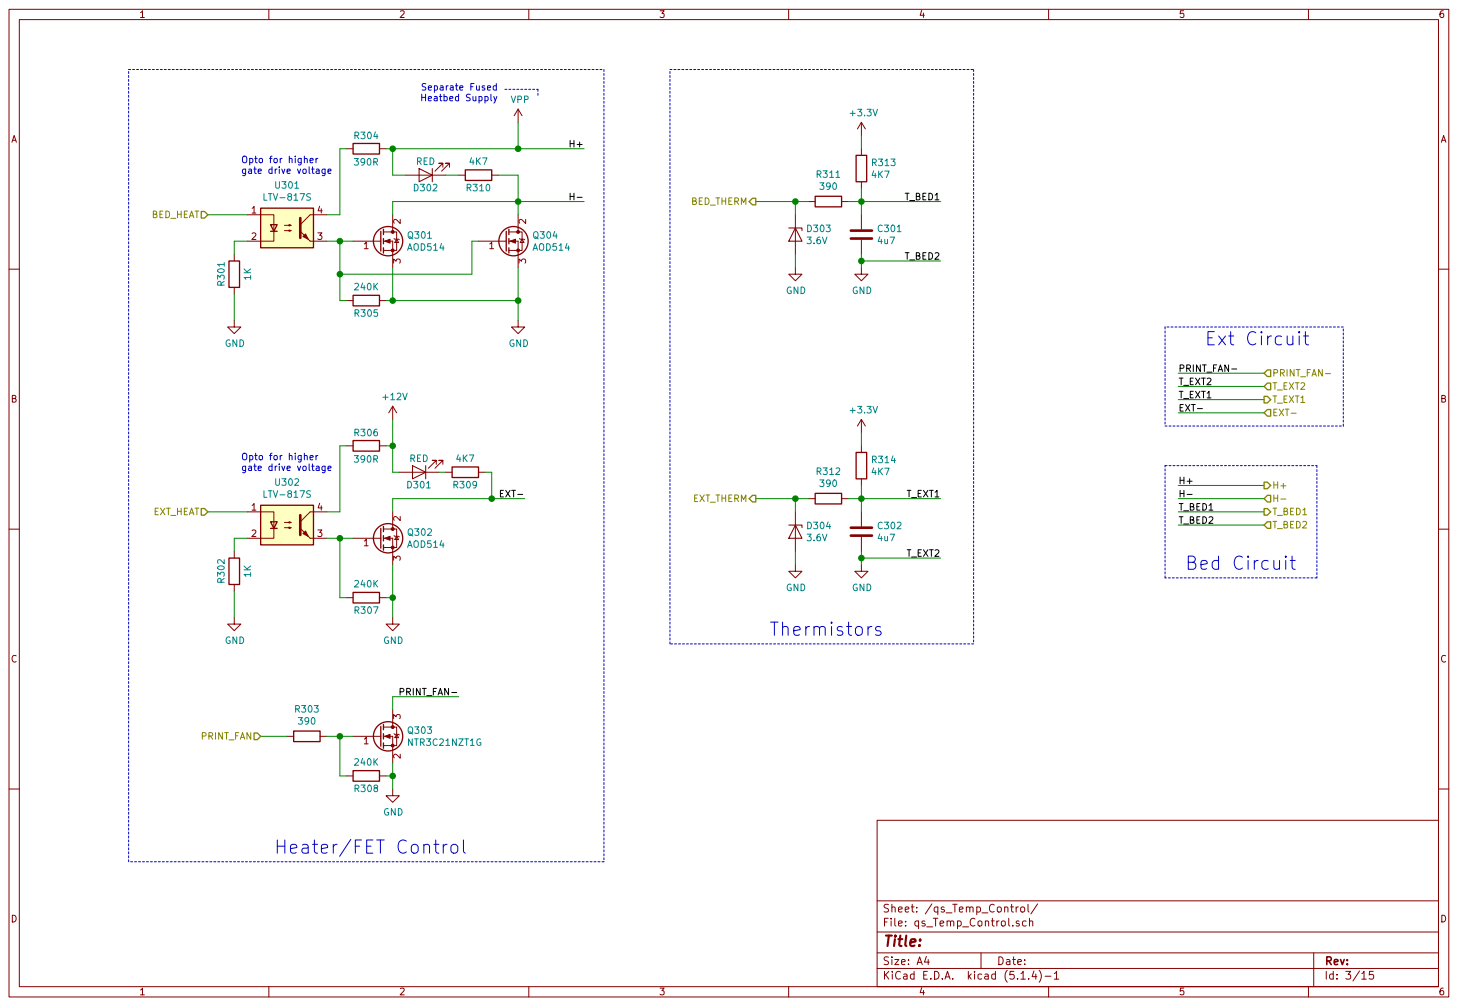
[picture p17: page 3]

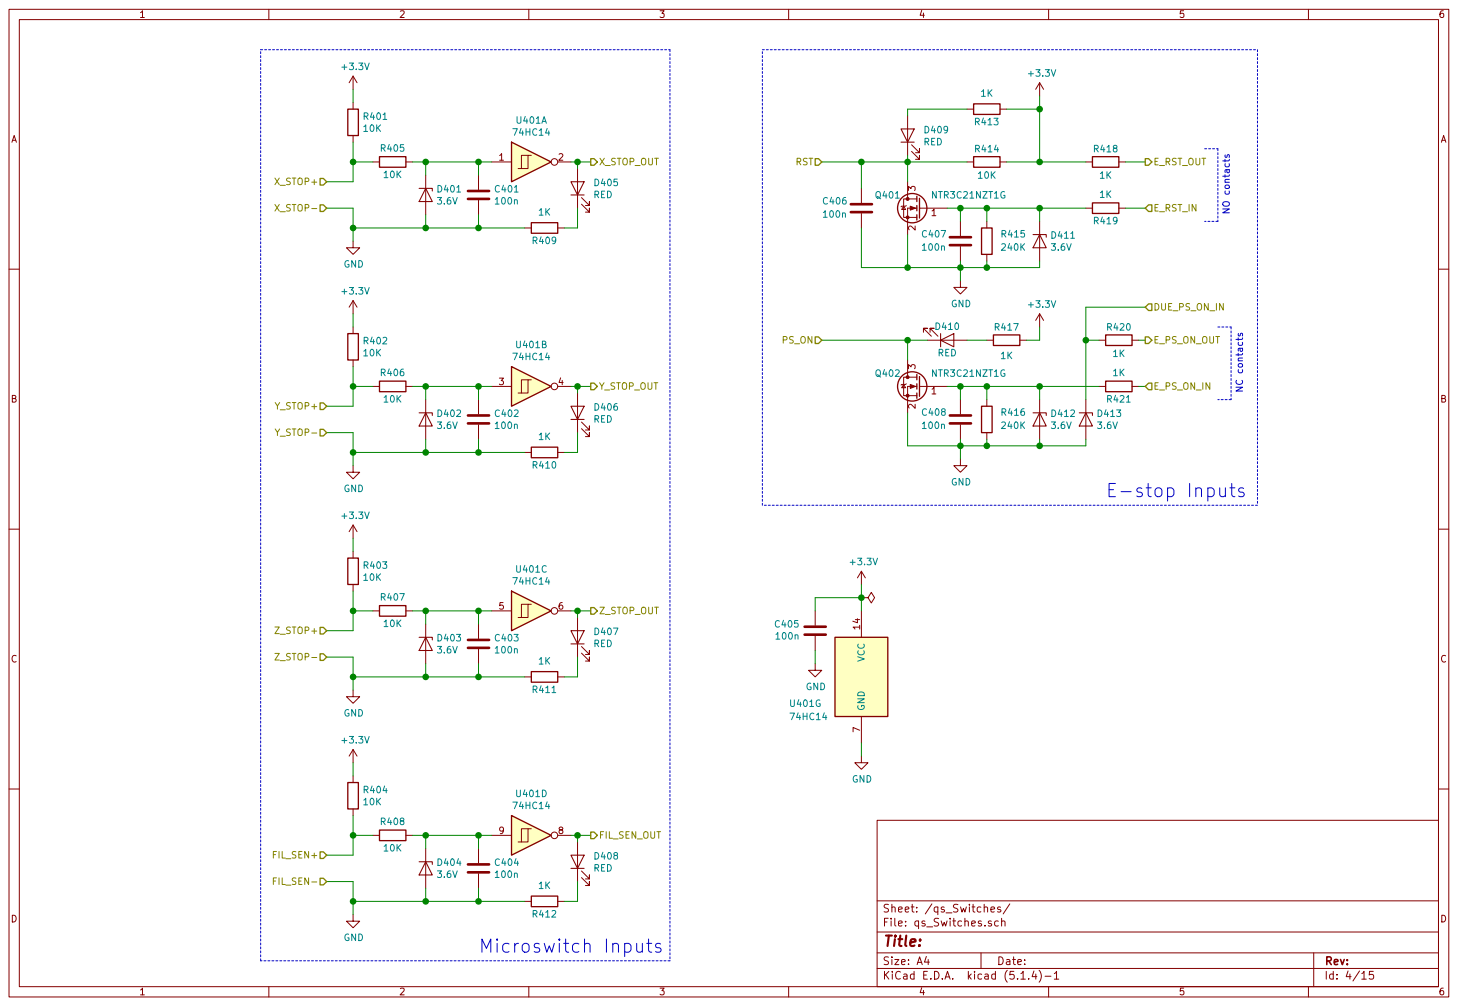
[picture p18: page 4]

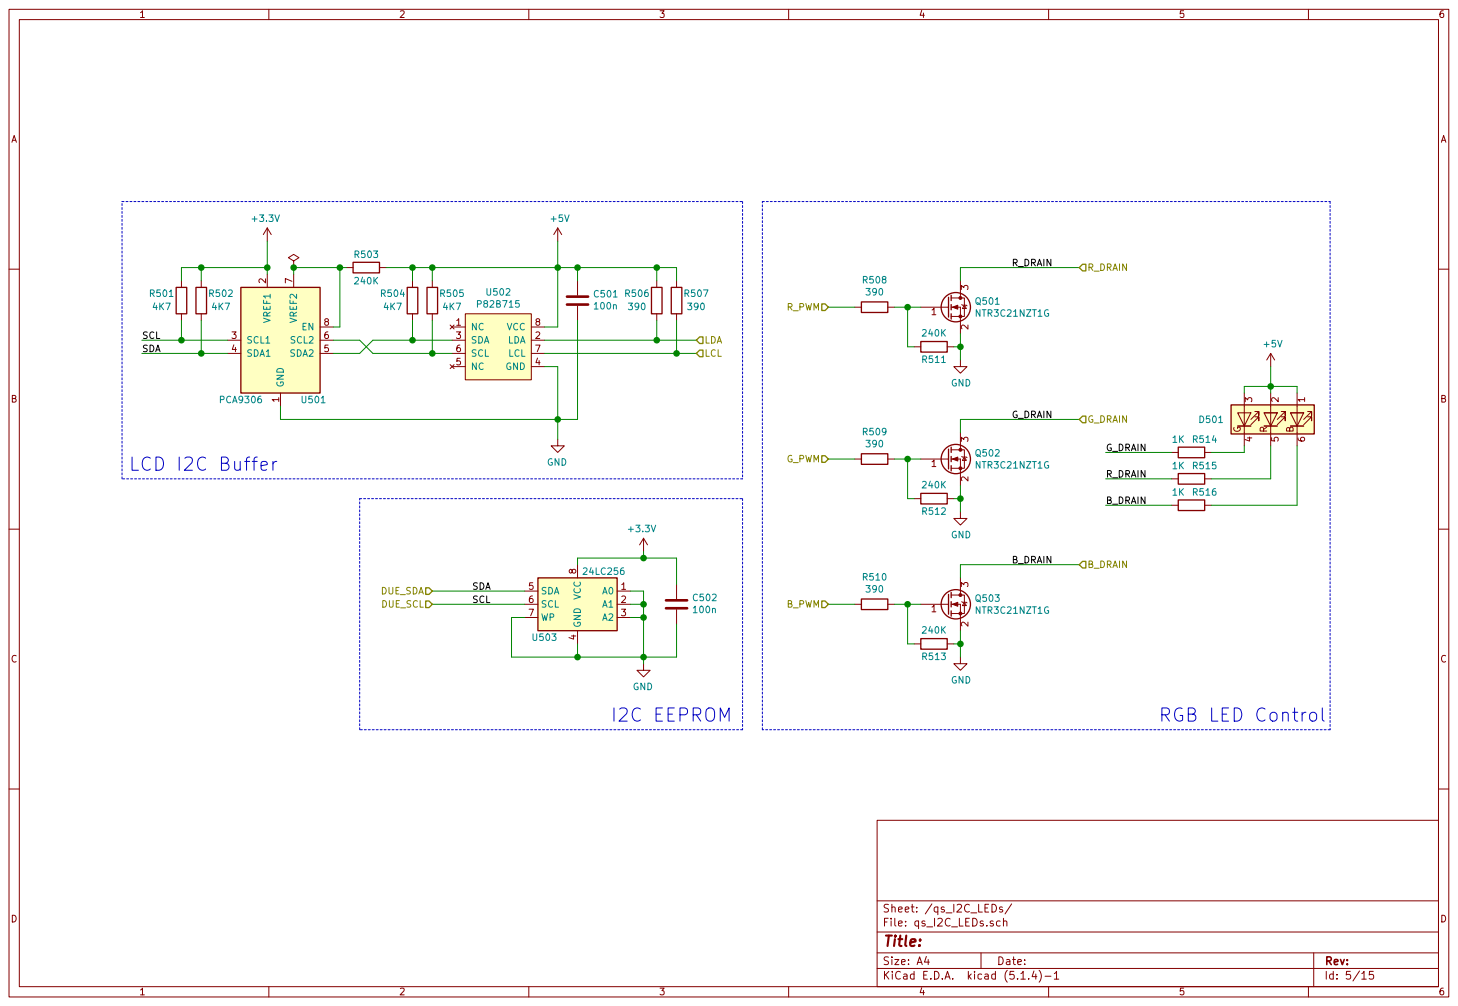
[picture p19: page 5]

4 SDA 5 SCL 6 WP 7 VCC

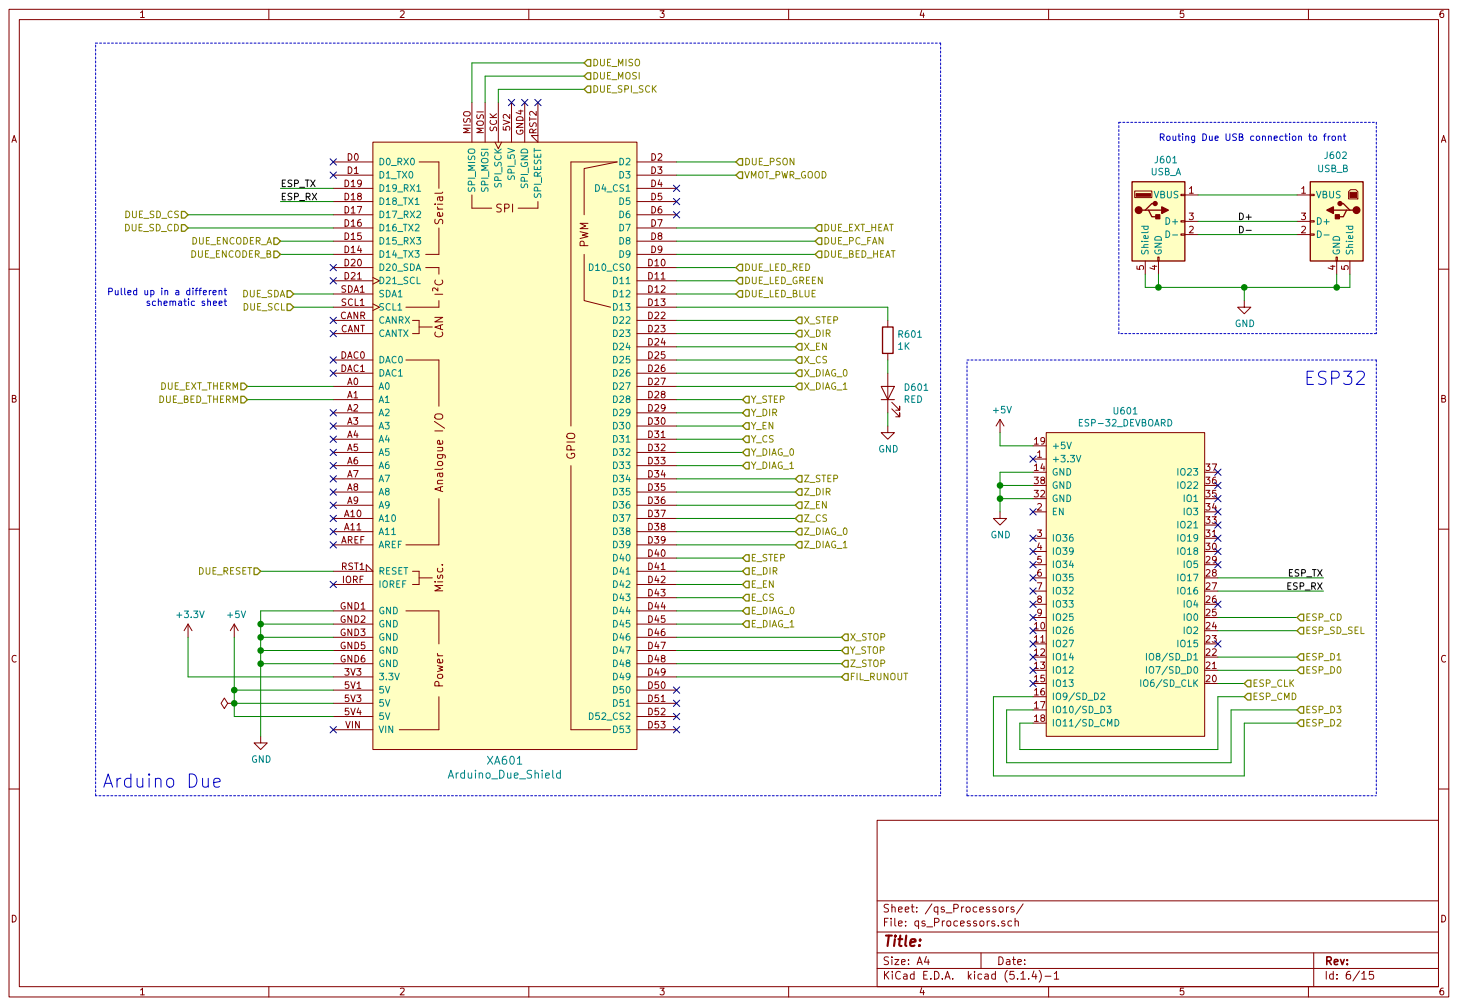
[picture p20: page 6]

Routing Due USB connection to front

Pulled up in a different schematic sheet


74HC245 GND GND GND GND GND GND

All of this buffering/switch circuitry is due to the
power rail sequencing requirements of the StepSticks.

All control signals to the stepsticks can only be enabled
after the logic supply rail rises to its operational level.

The logic supply can only rise after the motor supply is
good (VMOT_GOOD input) and has to fall before the VMOT
(VBUS) goes low. To turn VMOT off, we have to float
PS_ON, disabling the optocoupler. VMOT will stay high
a little due to rail capacitance, and should stay long
enough that the power sequencing works out.



instead of discrete diodes
for cost and space reasons


instead of discrete diodes
for cost and space reasons


9 | 10
11 | 12
13 | 14
15 | 16
17 | 18
19 | 20
21 | 22
23 | 24
25 | 26




Hotend Fan Using diode bridges instead
instead of discrete diodes
for cost and space reasons


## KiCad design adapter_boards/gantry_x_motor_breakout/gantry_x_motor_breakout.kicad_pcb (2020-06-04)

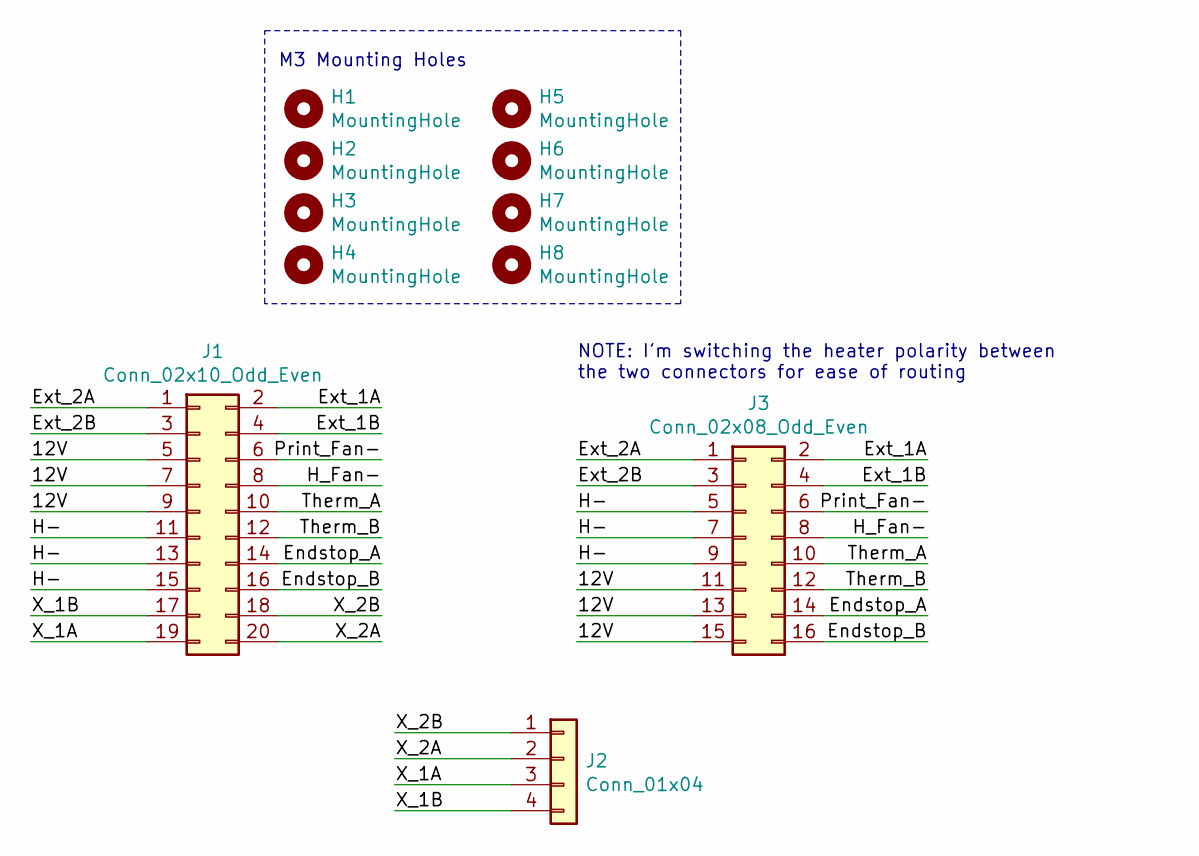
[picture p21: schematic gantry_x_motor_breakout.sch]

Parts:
H1, H2, H3, H4, H5, H6, H7, H8: MountingHole; MountingHole_3.2mm_M3_Pad
J1: Conn_02x10_Odd_Even; IDC-Header_2x10_P2.54mm_Vertical
J2: Conn_01x04; JST_XH_B4B-XH-A_1x04_P2.50mm_Vertical
J3: Conn_02x08_Odd_Even; IDC-Header_2x08_P2.54mm_Vertical

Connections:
/12V: J1.5, J1.7, J1.9, J3.11, J3.13, J3.15
/Endstop_A: J1.14, J3.14
/Endstop_B: J1.16, J3.16
/Ext_1A: J1.2, J3.2
/Ext_1B: J1.4, J3.4
/Ext_2A: J1.1, J3.1
/Ext_2B: J1.3, J3.3
/H-: J1.11, J1.13, J1.15, J3.5, J3.7, J3.9
/H_Fan-: J1.8, J3.8
/Print_Fan-: J1.6, J3.6
/Therm_A: J1.10, J3.10
/Therm_B: J1.12, J3.12
/X_1A: J1.19, J2.3
/X_1B: J1.17, J2.4
/X_2A: J1.20, J2.2
/X_2B: J1.18, J2.1

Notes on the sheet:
M3 Mounting Holes
NOTE: I'm switching the heater polarity between the two connectors for ease of routing

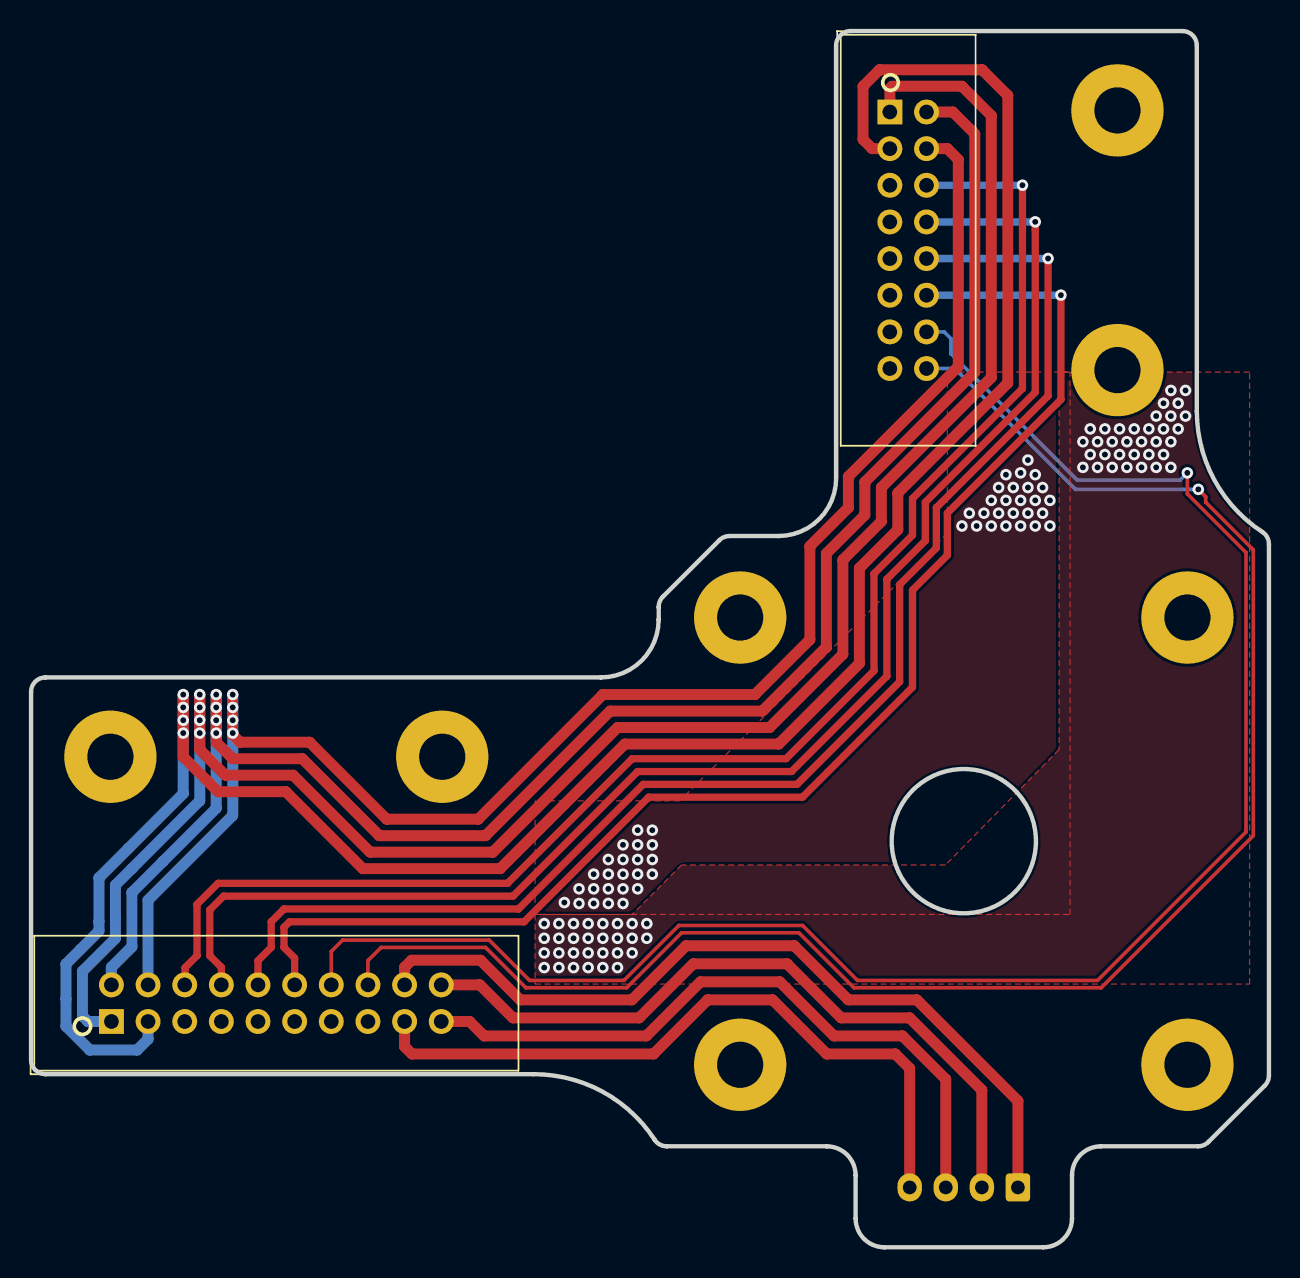
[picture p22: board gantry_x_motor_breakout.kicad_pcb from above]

Board: 2 copper layers, 85.8 x 84.3 mm, 11 parts (1 on the bottom side), 16 nets.

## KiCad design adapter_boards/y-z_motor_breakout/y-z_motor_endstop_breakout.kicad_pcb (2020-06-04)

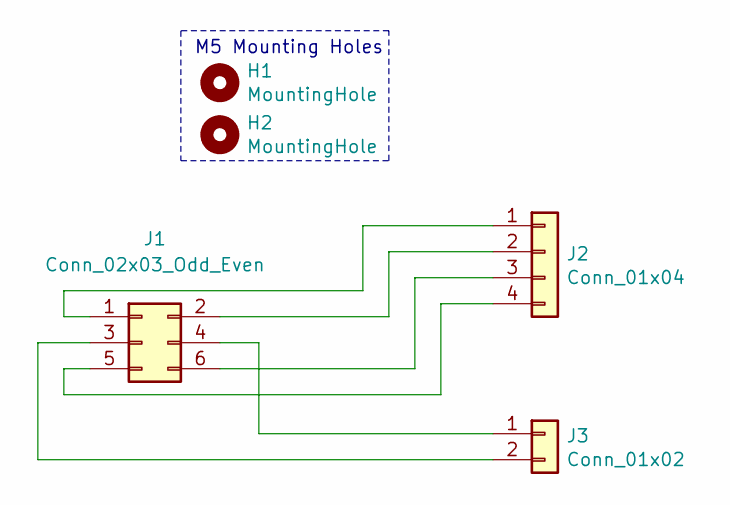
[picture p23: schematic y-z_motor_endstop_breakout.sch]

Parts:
H1, H2: MountingHole; MountingHole_5.3mm_M5_Pad
J1: Conn_02x03_Odd_Even; IDC-Header_2x03_P2.54mm_Vertical
J2: Conn_01x04; JST_XH_B4B-XH-A_1x04_P2.50mm_Vertical
J3: Conn_01x02; JST_XH_B2B-XH-A_1x02_P2.50mm_Vertical

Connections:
unnamed: J1.1, J2.1
unnamed: J1.2, J2.2
unnamed: J1.3, J3.2
unnamed: J1.4, J3.1
unnamed: J1.5, J2.4
unnamed: J1.6, J2.3

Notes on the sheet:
M5 Mounting Holes

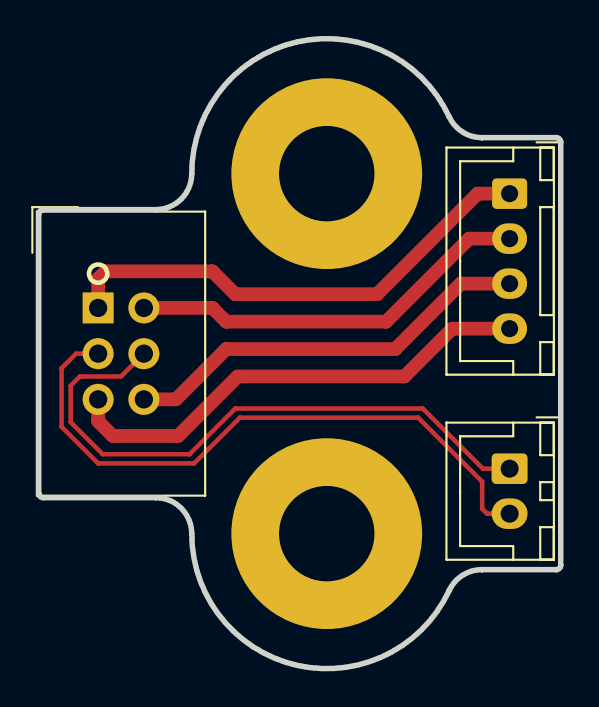
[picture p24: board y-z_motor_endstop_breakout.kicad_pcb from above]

Board: 2 copper layers, 29.0 x 35.0 mm, 5 parts (0 on the bottom side), 6 nets.

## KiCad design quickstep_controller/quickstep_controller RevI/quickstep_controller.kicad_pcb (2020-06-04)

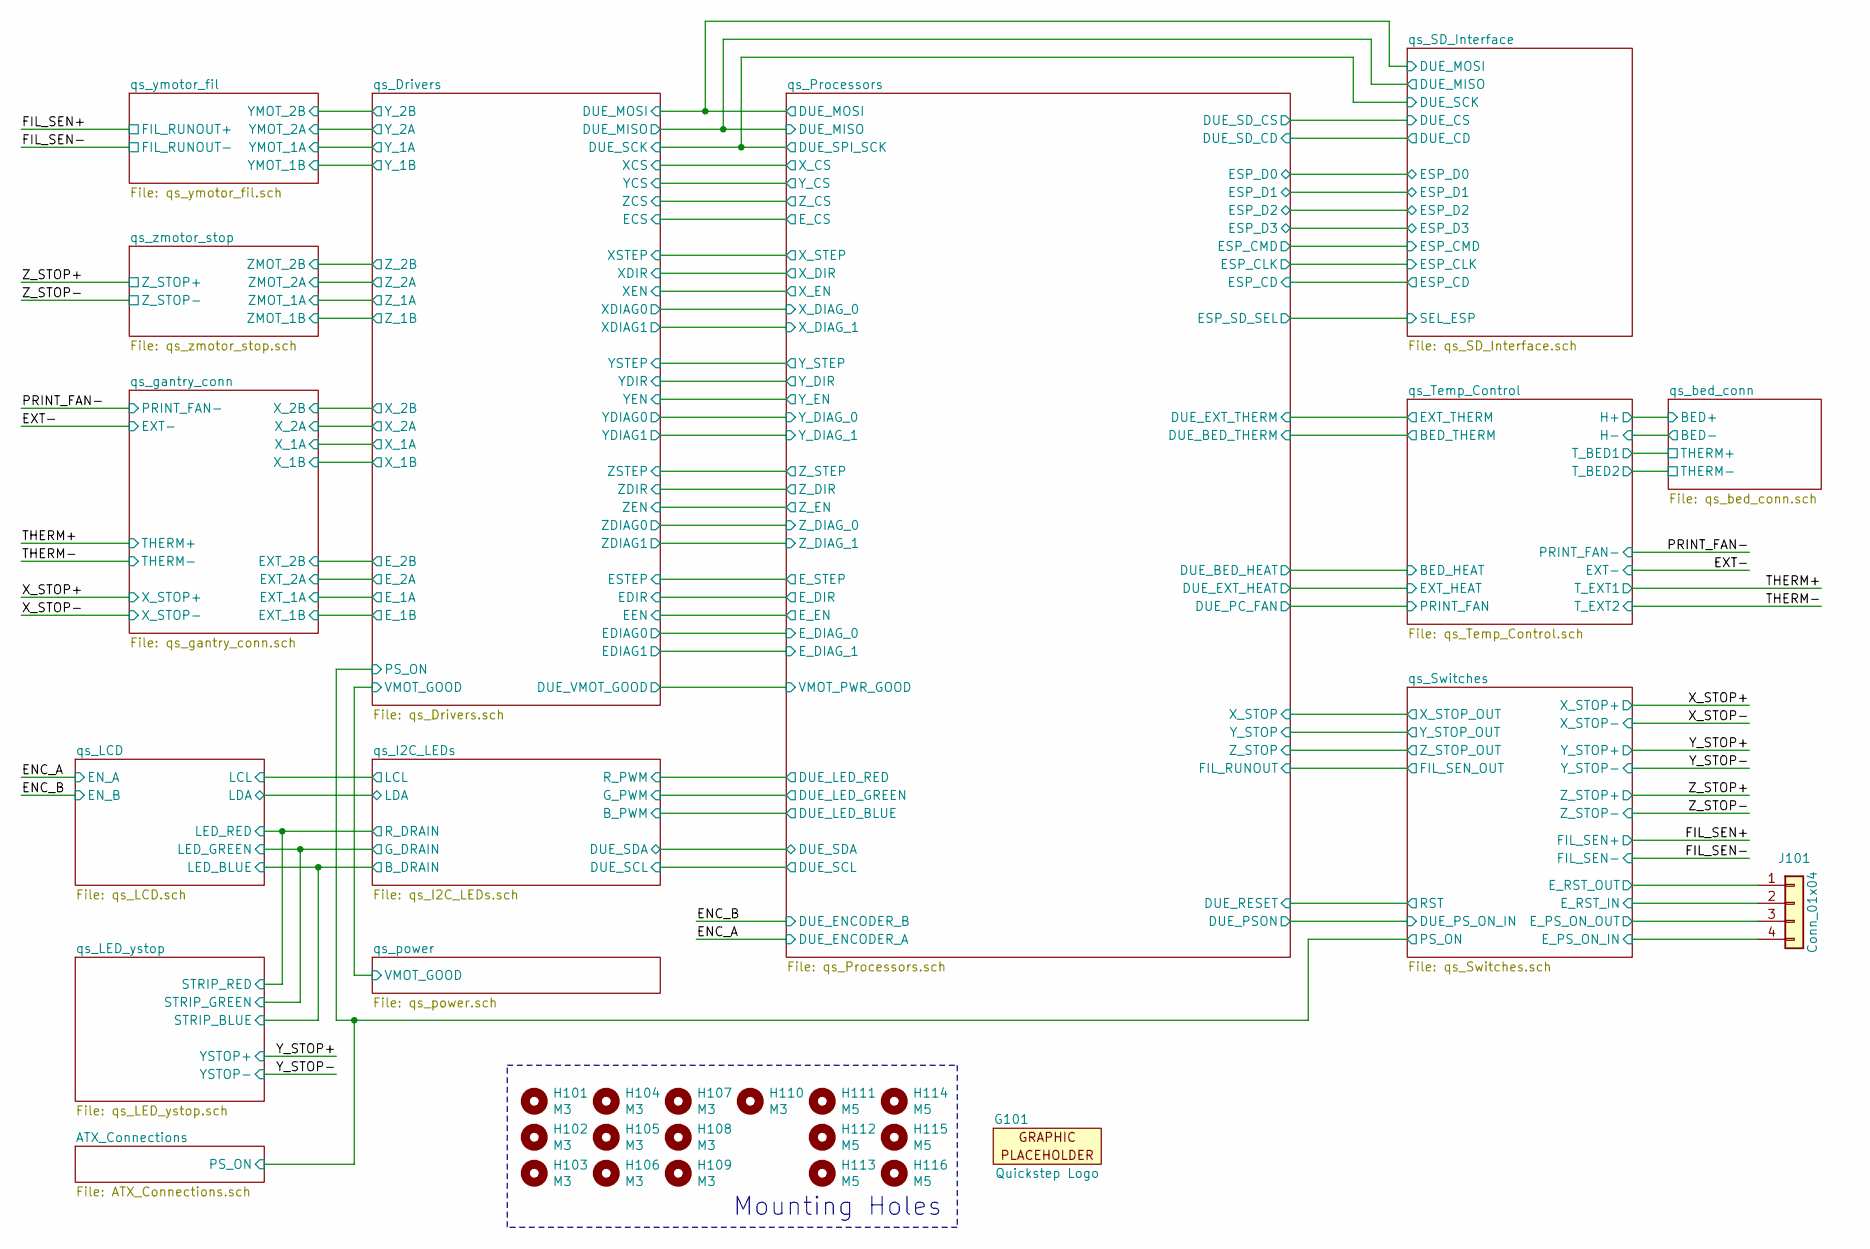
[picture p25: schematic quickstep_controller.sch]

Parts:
G101: Quickstep Logo; qs_logo
H101, H102, H103, H104, H105, H106, H107, H108, H109, H110: M3; MountingHole_3.2mm_M3_Pad
H111, H112, H113, H114, H115, H116: M5; MountingHole_5.3mm_M5_Pad
J101: Conn_01x04; JST_XH_B4B-XH-A_1x04_P2.50mm_Vertical

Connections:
/qs_Switches/E_PS_ON_IN: J101.4; also elsewhere on the board
/qs_Switches/E_PS_ON_OUT: J101.3; also elsewhere on the board
/qs_Switches/E_RST_IN: J101.2; also elsewhere on the board
/qs_Switches/E_RST_OUT: J101.1; also elsewhere on the board

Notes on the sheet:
Mounting Holes

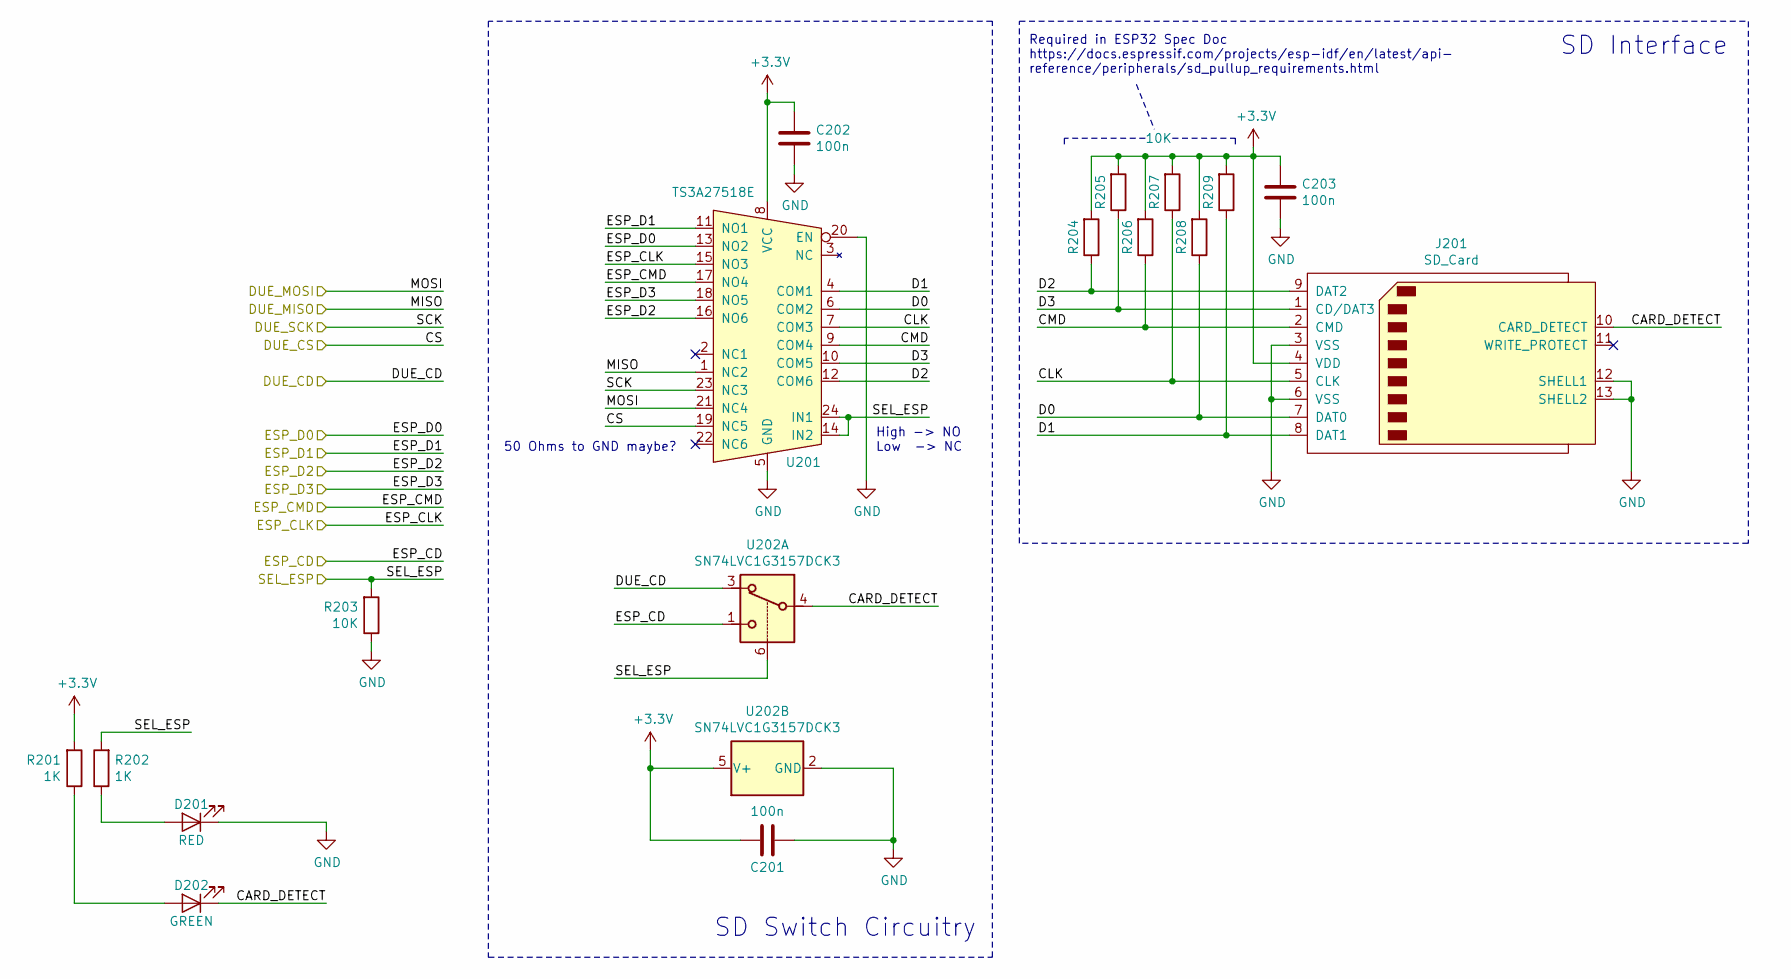
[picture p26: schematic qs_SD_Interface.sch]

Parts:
C201, C202, C203: 100n; C_0603_1608Metric_Pad1.05x0.95mm_HandSolder
D201: RED; LED_0603_1608Metric_Pad1.05x0.95mm_HandSolder
D202: GREEN; LED_0603_1608Metric_Pad1.05x0.95mm_HandSolder
J201: SD_Card; SD_TE_2041021; Part No. 2041021-4
R201, R202: 1K; R_0603_1608Metric_Pad1.05x0.95mm_HandSolder
R203, R204, R205, R206, R207, R208, R209: 10K; R_0603_1608Metric_Pad1.05x0.95mm_HandSolder
U201: TS3A27518E; TSSOP-24_4.4x7.8mm_P0.65mm
U202: SN74LVC1G3157DCK3; SOT-363_SC-70-6

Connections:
+3V3: C201.2, C202.1, C203.1, J201.4 (VDD), R201.2, R204.2, R205.2, R206.2, R207.2, R208.2, R209.2, U201.8 (VCC), U202.5 (V+); also elsewhere on the board
/qs_Drivers/DUE_MISO: U201.1 (NC2); also elsewhere on the board
/qs_Drivers/DUE_MOSI: U201.21 (NC4); also elsewhere on the board
/qs_Drivers/DUE_SCK: U201.23 (NC3); also elsewhere on the board
/qs_Processors/ESP_CD: U202.1; also elsewhere on the board
/qs_Processors/ESP_CLK: U201.15 (NO3); also elsewhere on the board
/qs_Processors/ESP_CMD: U201.17 (NO4); also elsewhere on the board
/qs_Processors/ESP_D0: U201.13 (NO2); also elsewhere on the board
/qs_Processors/ESP_D1: U201.11 (NO1); also elsewhere on the board
/qs_Processors/ESP_D2: U201.16 (NO6); also elsewhere on the board
/qs_Processors/ESP_D3: U201.18 (NO5); also elsewhere on the board
/qs_Processors/ESP_SD_SEL: R202.2, R203.2, U201.14 (IN2), U201.24 (IN1), U202.6; also elsewhere on the board
/qs_SD_Interface/CARD_DETECT: D202.1 (K), J201.10 (CARD_DETECT), U202.4
/qs_SD_Interface/CLK: J201.5 (CLK), R207.1, U201.7 (COM3)
/qs_SD_Interface/CMD: J201.2 (CMD), R206.1, U201.9 (COM4)
/qs_SD_Interface/D0: J201.7 (DAT0), R208.1, U201.6 (COM2)
/qs_SD_Interface/D1: J201.8 (DAT1), R209.1, U201.4 (COM1)
/qs_SD_Interface/D2: J201.9 (DAT2), R204.1, U201.12 (COM6)
/qs_SD_Interface/D3: J201.1 (CD/DAT3), R205.1, U201.10 (COM5)
/qs_SD_Interface/DUE_CD: U202.3; also elsewhere on the board
/qs_SD_Interface/DUE_CS: U201.19 (NC5); also elsewhere on the board
GND: C201.1, C202.2, C203.2, D201.1 (K), J201.3 (VSS), J201.6 (VSS), J201.12 (SHELL1), J201.13 (SHELL2), R203.1, U201.5 (GND), U201.20 (EN), U202.2 (GND); also elsewhere on the board
unnamed: D201.2 (A), R202.1
unnamed: D202.2 (A), R201.1

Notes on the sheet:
High -> NO Low -> NC
50 Ohms to GND maybe?
SD Switch Circuitry
SD Interface
Required in ESP32 Spec Doc https://docs.espressif.com/projects/esp-idf/en/latest/api- reference/peripherals/sd_pullup_requirements.html

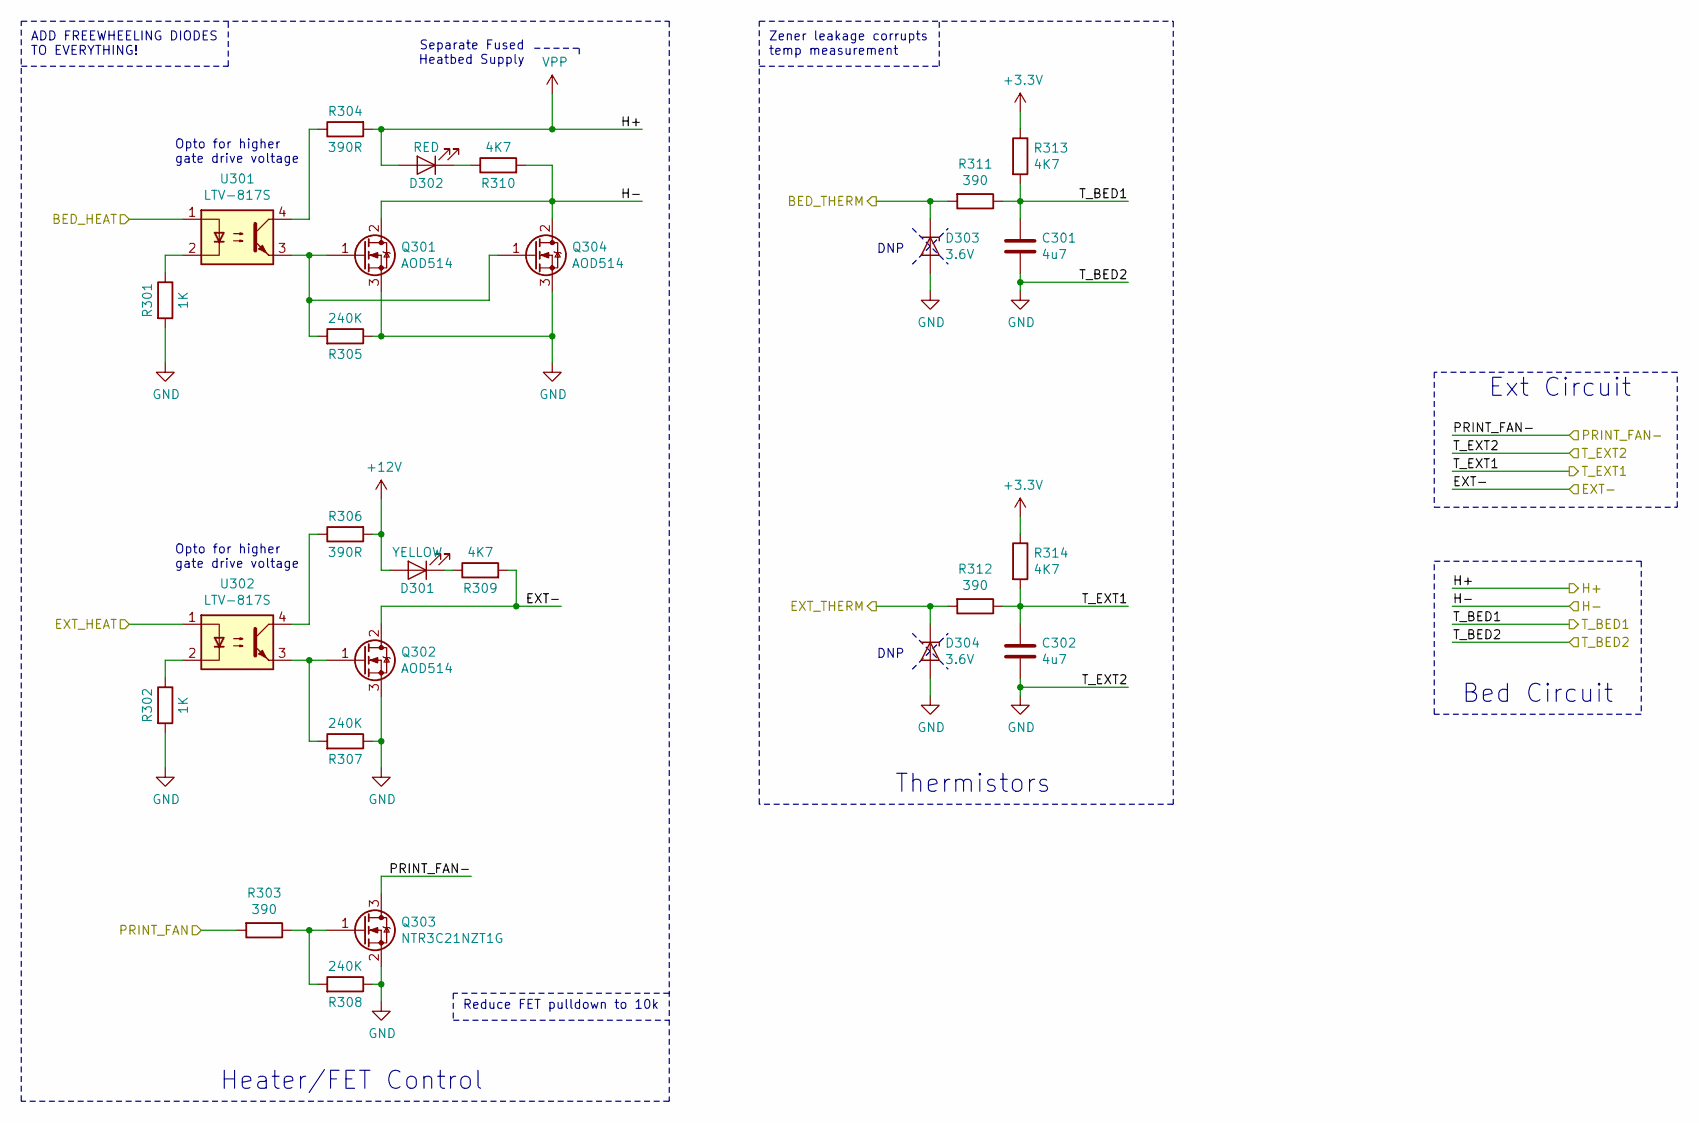
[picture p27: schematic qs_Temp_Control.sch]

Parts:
C301, C302: 4u7; C_0805_2012Metric_Pad1.15x1.40mm_HandSolder
D301: YELLOW; LED_0603_1608Metric_Pad1.05x0.95mm_HandSolder
D302: RED; LED_0603_1608Metric_Pad1.05x0.95mm_HandSolder
D303, D304: 3.6V; D_SOD-323_HandSoldering; Part No. MM3Z3V6T1G
Q301, Q302, Q304: AOD514; TO-252-2
Q303: NTR3C21NZT1G; SOT-23_Handsoldering
R301, R302: 1K; R_0603_1608Metric_Pad1.05x0.95mm_HandSolder
R303, R311, R312: 390; R_0603_1608Metric_Pad1.05x0.95mm_HandSolder
R304, R306: 390R; R_0603_1608Metric_Pad1.05x0.95mm_HandSolder
R305, R307, R308: 240K; R_0603_1608Metric_Pad1.05x0.95mm_HandSolder
R309, R310, R313, R314: 4K7; R_0603_1608Metric_Pad1.05x0.95mm_HandSolder
U301, U302: LTV-817S; SMDIP-4_W9.53mm

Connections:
+3V3: R313.1, R314.1; also elsewhere on the board
+12V: D301.2 (A), R306.2; also elsewhere on the board
/EXT-: Q302.2 (D), R309.2; also elsewhere on the board
/PRINT_FAN-: Q303.3 (D); also elsewhere on the board
/THERM+: C302.1, R312.1, R314.2; also elsewhere on the board
/qs_Processors/DUE_EXT_HEAT: U302.1; also elsewhere on the board
/qs_Processors/DUE_EXT_THERM: D304.1 (K), R312.2; also elsewhere on the board
/qs_Processors/DUE_PC_FAN: R303.2; also elsewhere on the board
/qs_Temp_Control/BED_HEAT: U301.1; also elsewhere on the board
/qs_Temp_Control/BED_THERM: D303.1 (K), R311.2; also elsewhere on the board
/qs_bed_conn/BED-: Q301.2 (D), Q304.2 (D), R310.2; also elsewhere on the board
/qs_bed_conn/THERM+: C301.1, R311.1, R313.2; also elsewhere on the board
GND: C301.2, C302.2, D303.2 (A), D304.2 (A), Q301.3 (S), Q302.3 (S), Q303.2 (S), Q304.3 (S), R301.2, R302.2, R305.1, R307.1, R308.1; also elsewhere on the board
unnamed: D301.1 (K), R309.1
unnamed: D302.1 (K), R310.1
unnamed: Q301.1 (G), Q304.1 (G), R305.2, U301.3
unnamed: Q302.1 (G), R307.2, U302.3
unnamed: Q303.1 (G), R303.1, R308.2
unnamed: R301.1, U301.2
unnamed: R302.1, U302.2
unnamed: R304.1, U301.4
unnamed: R306.1, U302.4
VPP: D302.2 (A), R304.2; also elsewhere on the board

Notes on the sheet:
Opto for higher gate drive voltage
Heater/FET Control
Thermistors
Bed Circuit
Ext Circuit
Separate Fused Heatbed Supply
Reduce FET pulldown to 10k
DNP
ADD FREEWHEELING DIODES TO EVERYTHING!
Zener leakage corrupts temp measurement

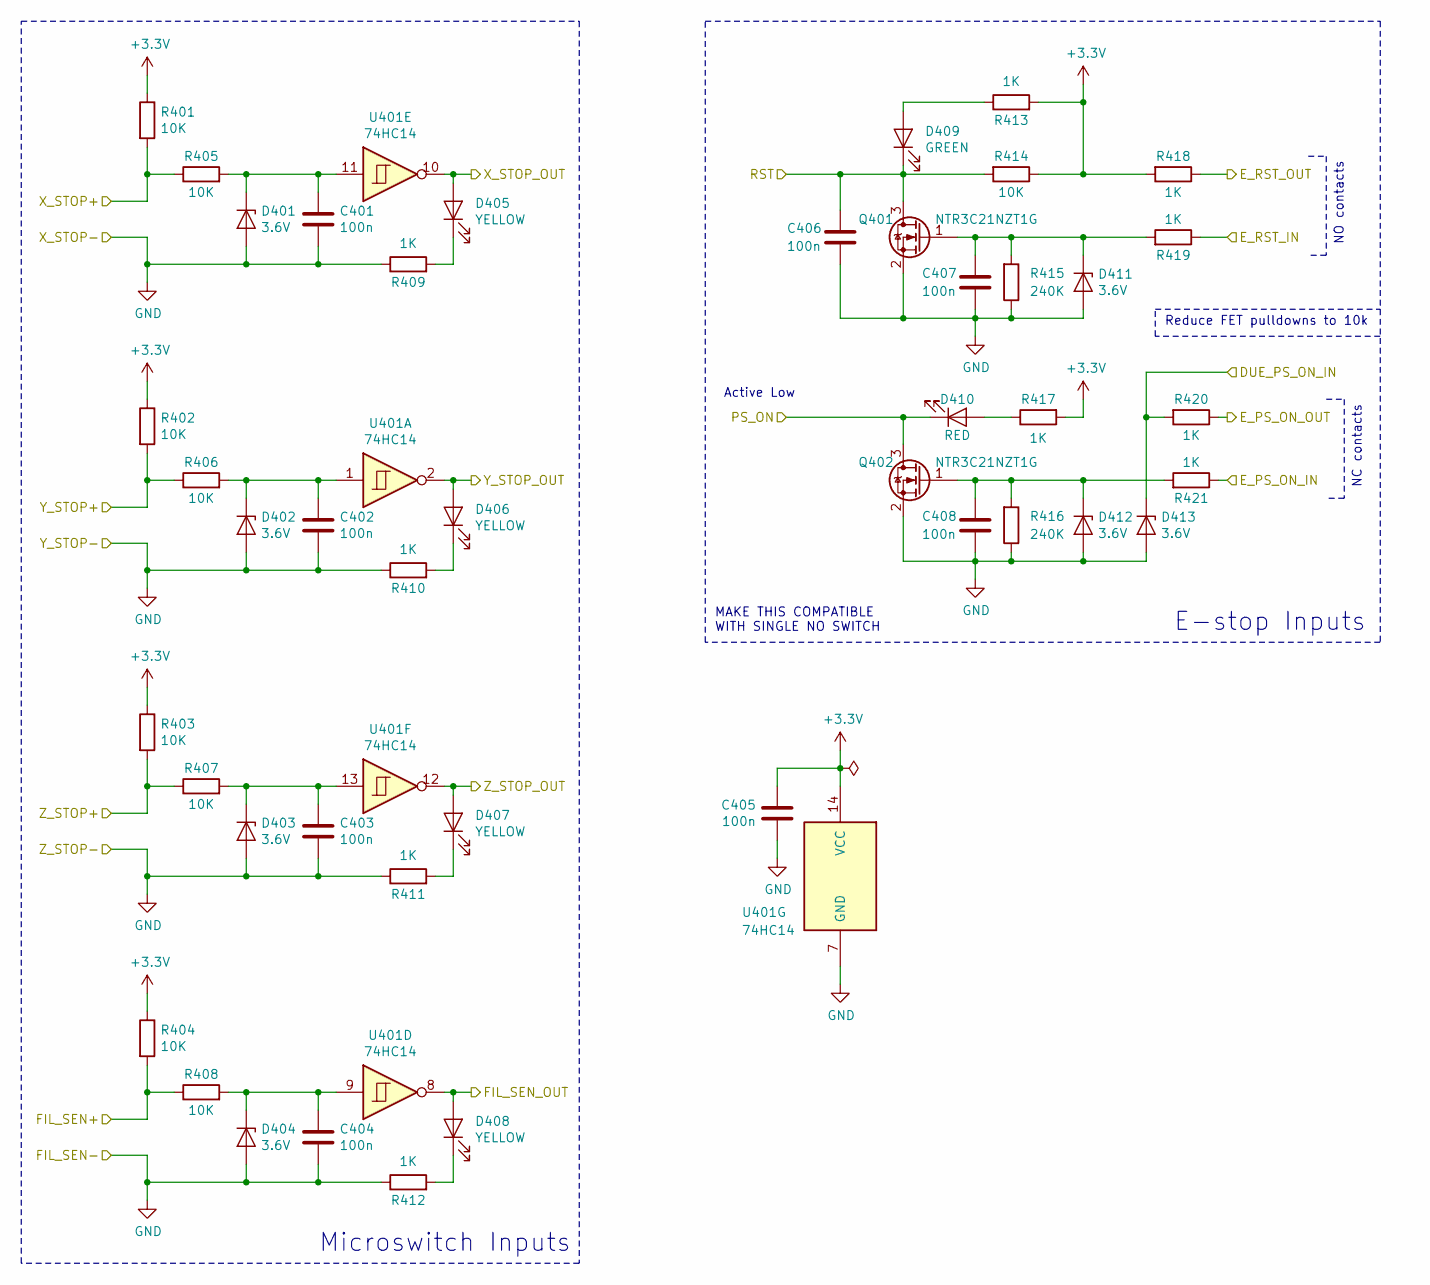
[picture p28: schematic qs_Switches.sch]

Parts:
C401, C402, C403, C404, C405, C406, C407, C408: 100n; C_0603_1608Metric_Pad1.05x0.95mm_HandSolder
D401, D402, D403, D404, D411, D412, D413: 3.6V; D_SOD-323_HandSoldering; Part No. MM3Z3V6T1G
D405, D406, D407, D408: YELLOW; LED_0603_1608Metric_Pad1.05x0.95mm_HandSolder
D409: GREEN; LED_0603_1608Metric_Pad1.05x0.95mm_HandSolder
D410: RED; LED_0603_1608Metric_Pad1.05x0.95mm_HandSolder
Q401, Q402: NTR3C21NZT1G; SOT-23_Handsoldering
R401, R402, R403, R404, R405, R406, R407, R408, R414: 10K; R_0603_1608Metric_Pad1.05x0.95mm_HandSolder
R409, R410, R411, R412, R413, R417, R418, R419, R420, R421: 1K; R_0603_1608Metric_Pad1.05x0.95mm_HandSolder
R415, R416: 240K; R_0603_1608Metric_Pad1.05x0.95mm_HandSolder
U401: 74HC14; TSSOP-14_4.4x5mm_P0.65mm

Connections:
+3V3: C405.2, R401.1, R402.1, R403.1, R404.1, R413.2, R414.1, R417.2, R418.2, U401.14 (VCC); also elsewhere on the board
/ATX_Connections/PS_ON: D410.1 (K), Q402.3 (D); also elsewhere on the board
/FIL_SEN+: R404.2, R408.1; also elsewhere on the board
/X_STOP+: R401.2, R405.1; also elsewhere on the board
/Y_STOP+: R402.2, R406.1; also elsewhere on the board
/Z_STOP+: R403.2, R407.1; also elsewhere on the board
/qs_Processors/DUE_PSON: D413.1 (K), R420.2; also elsewhere on the board
/qs_Processors/DUE_RESET: C406.2, D409.1 (K), Q401.3 (D), R414.2; also elsewhere on the board
/qs_Processors/FIL_RUNOUT: D408.2 (A), U401.8; also elsewhere on the board
/qs_Processors/X_STOP: D405.2 (A), U401.10; also elsewhere on the board
/qs_Processors/Y_STOP: D406.2 (A), U401.2; also elsewhere on the board
/qs_Processors/Z_STOP: D407.2 (A), U401.12; also elsewhere on the board
/qs_Switches/E_PS_ON_IN: R421.1; also elsewhere on the board
/qs_Switches/E_PS_ON_OUT: R420.1; also elsewhere on the board
/qs_Switches/E_RST_IN: R419.1; also elsewhere on the board
/qs_Switches/E_RST_OUT: R418.1; also elsewhere on the board
GND: C401.2, C402.2, C403.2, C404.2, C405.1, C406.1, C407.1, C408.1, D401.2 (A), D402.2 (A), D403.2 (A), D404.2 (A), D411.2 (A), D412.2 (A), D413.2 (A), Q401.2 (S), Q402.2 (S), R409.1, R410.1, R411.1, R412.1, R415.1, R416.1, U401.7 (GND); also elsewhere on the board
unnamed: C401.1, D401.1 (K), R405.2, U401.11
unnamed: C402.1, D402.1 (K), R406.2, U401.1
unnamed: C403.1, D403.1 (K), R407.2, U401.13
unnamed: C404.1, D404.1 (K), R408.2, U401.9
unnamed: C407.2, D411.1 (K), Q401.1 (G), R415.2, R419.2
unnamed: C408.2, D412.1 (K), Q402.1 (G), R416.2, R421.2
unnamed: D405.1 (K), R409.2
unnamed: D406.1 (K), R410.2
unnamed: D407.1 (K), R411.2
unnamed: D408.1 (K), R412.2
unnamed: D409.2 (A), R413.1
unnamed: D410.2 (A), R417.1

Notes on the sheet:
Microswitch Inputs
NO contacts
NC contacts
E-stop Inputs
Active Low
Reduce FET pulldowns to 10k
MAKE THIS COMPATIBLE WITH SINGLE NO SWITCH

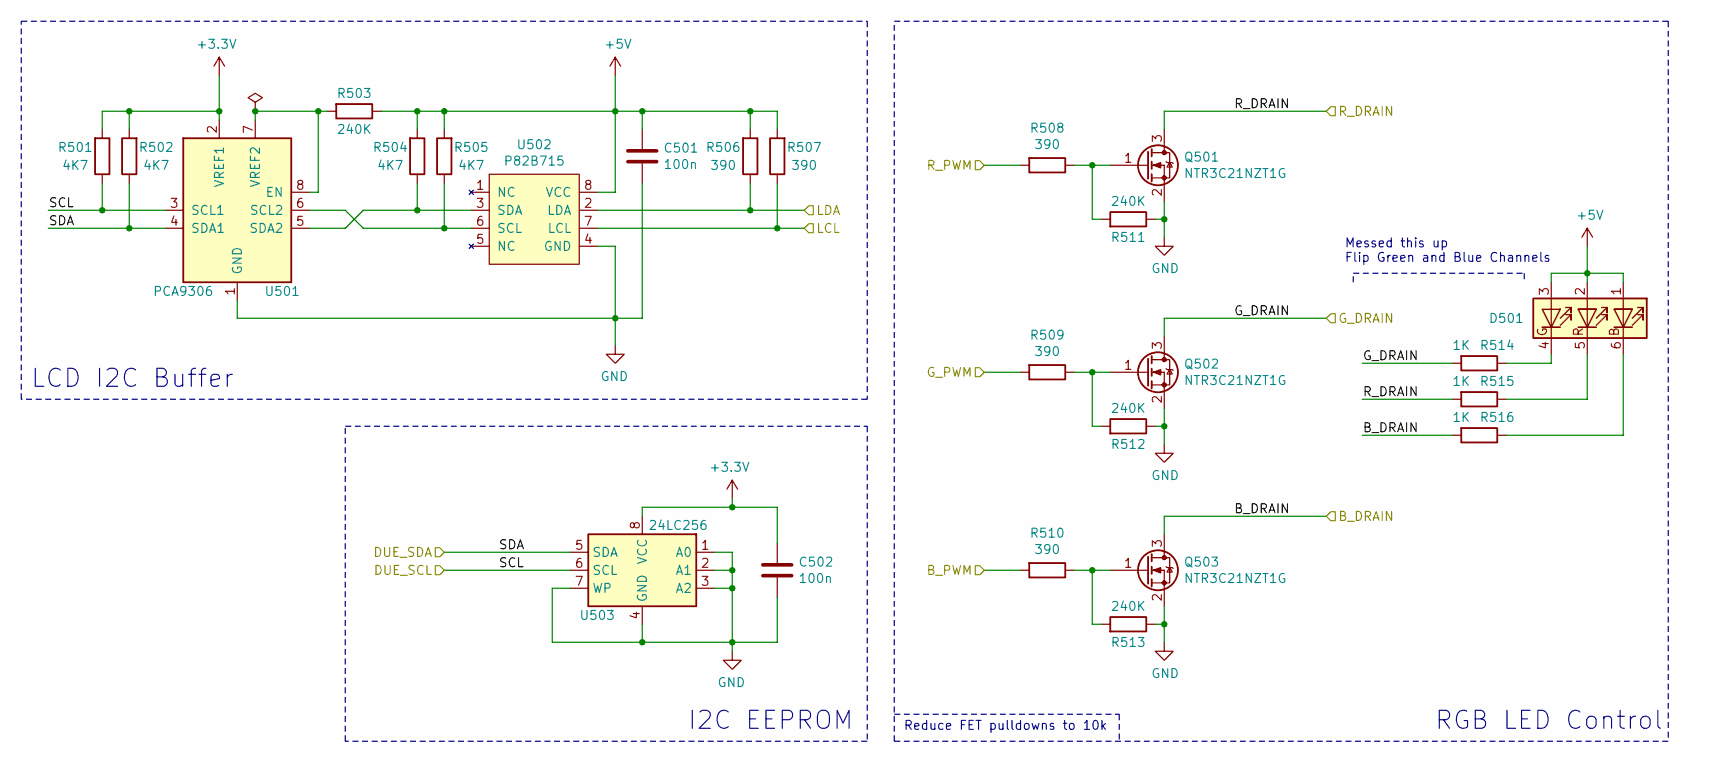
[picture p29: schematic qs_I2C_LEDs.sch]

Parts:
C501, C502: 100n; C_0603_1608Metric_Pad1.05x0.95mm_HandSolder
D501: 150505M173300; LED_RGB_5050-6; Part No. 150505M173300
Q501, Q502, Q503: NTR3C21NZT1G; SOT-23_Handsoldering
R501, R502, R504, R505: 4K7; R_0603_1608Metric_Pad1.05x0.95mm_HandSolder
R503, R511, R512, R513: 240K; R_0603_1608Metric_Pad1.05x0.95mm_HandSolder
R506, R507, R508, R509, R510: 390; R_0603_1608Metric_Pad1.05x0.95mm_HandSolder
R514, R515, R516: 1K; R_0603_1608Metric_Pad1.05x0.95mm_HandSolder
U501: PCA9306; SSOP-8_2.95x2.8mm_P0.65mm; Part No. PCA9306DCTR
U502: P82B715; SOIC-8_3.9x4.9mm_P1.27mm
U503: 24LC256; TSSOP-8_4.4x3mm_P0.65mm; Part No. 24LC256-I/ST

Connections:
+3V3: C502.2, R501.2, R502.2, U501.2 (VREF1), U503.8 (VCC); also elsewhere on the board
+5V: C501.2, D501.1 (BA), D501.2 (RA), D501.3 (GA), R503.1, R504.2, R505.2, R506.2, R507.2, U502.8 (VCC); also elsewhere on the board
/qs_I2C_LEDs/B_DRAIN: Q503.3 (D), R516.2; also elsewhere on the board
/qs_I2C_LEDs/B_PWM: R510.2; also elsewhere on the board
/qs_I2C_LEDs/DUE_SCL: R501.1, U501.3 (SCL1), U503.6 (SCL); also elsewhere on the board
/qs_I2C_LEDs/DUE_SDA: R502.1, U501.4 (SDA1), U503.5 (SDA); also elsewhere on the board
/qs_I2C_LEDs/G_DRAIN: Q502.3 (D), R514.2; also elsewhere on the board
/qs_I2C_LEDs/LCL: R507.1, U502.7 (LCL); also elsewhere on the board
/qs_I2C_LEDs/LDA: R506.1, U502.2 (LDA); also elsewhere on the board
/qs_LCD/LED_RED: Q501.3 (D), R515.2; also elsewhere on the board
/qs_Processors/DUE_LED_GREEN: R509.2; also elsewhere on the board
/qs_Processors/DUE_LED_RED: R508.2; also elsewhere on the board
GND: C501.1, C502.1, Q501.2 (S), Q502.2 (S), Q503.2 (S), R511.1, R512.1, R513.1, U501.1 (GND), U502.4 (GND), U503.1 (A0), U503.2 (A1), U503.3 (A2), U503.4 (GND), U503.7 (WP); also elsewhere on the board
unnamed: D501.4 (GK), R514.1
unnamed: D501.5 (RK), R515.1
unnamed: D501.6 (BK), R516.1
unnamed: Q501.1 (G), R508.1, R511.2
unnamed: Q502.1 (G), R509.1, R512.2
unnamed: Q503.1 (G), R510.1, R513.2
unnamed: R503.2, U501.7 (VREF2), U501.8 (EN)
unnamed: R504.1, U501.5 (SDA2), U502.3 (SDA)
unnamed: R505.1, U501.6 (SCL2), U502.6 (SCL)

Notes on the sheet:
RGB LED Control
I2C EEPROM
LCD I2C Buffer
Messed this up Flip Green and Blue Channels
Reduce FET pulldowns to 10k

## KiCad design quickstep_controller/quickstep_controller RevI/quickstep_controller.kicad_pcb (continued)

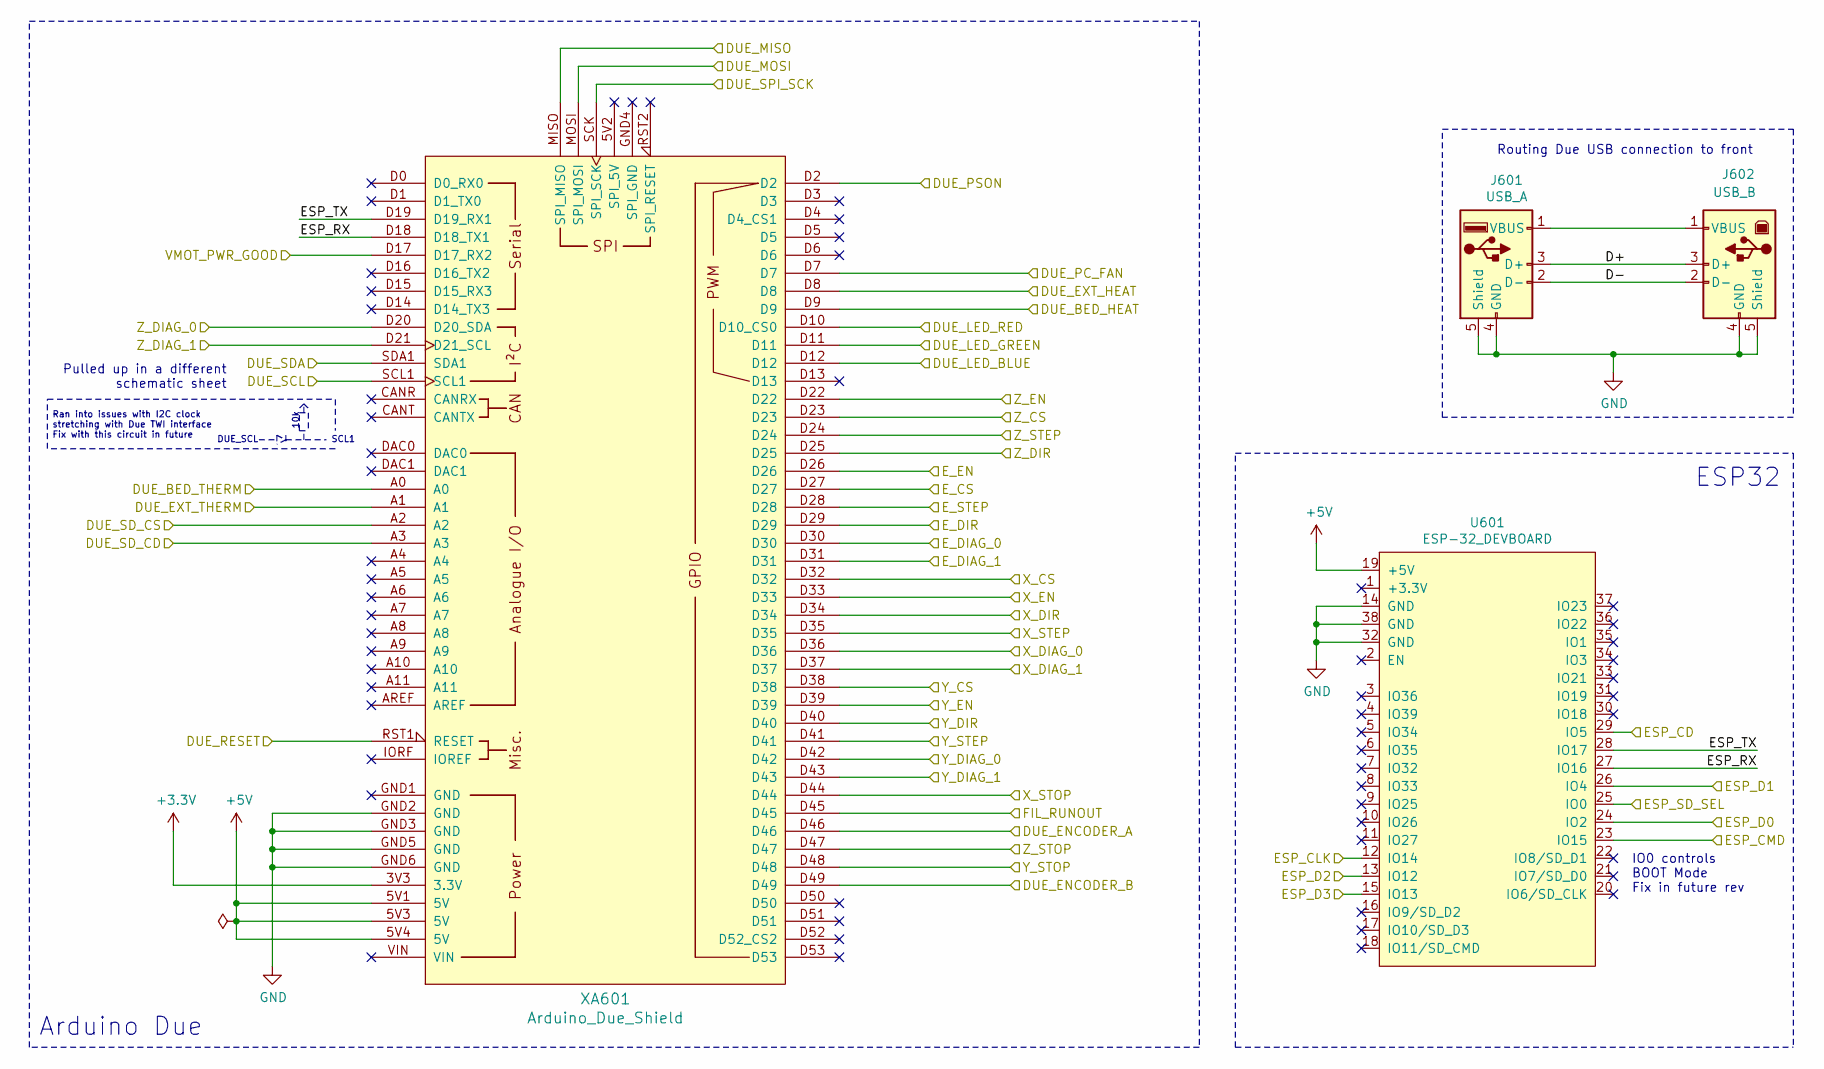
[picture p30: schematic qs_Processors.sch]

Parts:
J601: USB_A; USB_Adapter
J602: USB_B; CUI_UJ2-BH-W1-TH; Part No. USB-B1HSB6
U601: ESP-32_DEVBOARD; ESP32
XA601: Arduino_Due_Shield; Arduino_Due_Shield_noHolesSilk

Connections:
+3V3: XA601.3V3 (3.3V); also elsewhere on the board
+5V: U601.19 (+5V), XA601.5V1 (5V), XA601.5V3 (5V), XA601.5V4 (5V); also elsewhere on the board
/ENC_A: XA601.D46; also elsewhere on the board
/ENC_B: XA601.D49; also elsewhere on the board
/qs_Drivers/DUE_MISO: XA601.MISO (SPI_MISO); also elsewhere on the board
/qs_Drivers/DUE_MOSI: XA601.MOSI (SPI_MOSI); also elsewhere on the board
/qs_Drivers/DUE_SCK: XA601.SCK (SPI_SCK); also elsewhere on the board
/qs_Drivers/DUE_VMOT_GOOD: XA601.D17 (D17_RX2); also elsewhere on the board
/qs_Drivers/ECS: XA601.D27; also elsewhere on the board
/qs_Drivers/EDIAG0: XA601.D30; also elsewhere on the board
/qs_Drivers/EDIAG1: XA601.D31; also elsewhere on the board
/qs_Drivers/EDIR: XA601.D29; also elsewhere on the board
/qs_Drivers/EEN: XA601.D26; also elsewhere on the board
/qs_Drivers/ESTEP: XA601.D28; also elsewhere on the board
/qs_Drivers/XCS: XA601.D32; also elsewhere on the board
/qs_Drivers/XDIAG0: XA601.D36; also elsewhere on the board
/qs_Drivers/XDIAG1: XA601.D37; also elsewhere on the board
/qs_Drivers/XDIR: XA601.D34; also elsewhere on the board
/qs_Drivers/XEN: XA601.D33; also elsewhere on the board
/qs_Drivers/XSTEP: XA601.D35; also elsewhere on the board
/qs_Drivers/YCS: XA601.D38; also elsewhere on the board
/qs_Drivers/YDIAG0: XA601.D42; also elsewhere on the board
/qs_Drivers/YDIAG1: XA601.D43; also elsewhere on the board
/qs_Drivers/YDIR: XA601.D40; also elsewhere on the board
/qs_Drivers/YEN: XA601.D39; also elsewhere on the board
/qs_Drivers/YSTEP: XA601.D41; also elsewhere on the board
/qs_Drivers/ZCS: XA601.D23; also elsewhere on the board
/qs_Drivers/ZDIAG0: XA601.D20 (D20_SDA); also elsewhere on the board
/qs_Drivers/ZDIAG1: XA601.D21 (D21_SCL); also elsewhere on the board
/qs_Drivers/ZDIR: XA601.D25; also elsewhere on the board
/qs_Drivers/ZEN: XA601.D22; also elsewhere on the board
/qs_Drivers/ZSTEP: XA601.D24; also elsewhere on the board
/qs_I2C_LEDs/B_PWM: XA601.D12; also elsewhere on the board
/qs_I2C_LEDs/DUE_SCL: XA601.SCL1; also elsewhere on the board
/qs_I2C_LEDs/DUE_SDA: XA601.SDA1; also elsewhere on the board
/qs_Processors/D+: J601.3 (D+), J602.3 (D+)
/qs_Processors/D-: J601.2 (D-), J602.2 (D-)
/qs_Processors/DUE_EXT_HEAT: XA601.D8; also elsewhere on the board
/qs_Processors/DUE_EXT_THERM: XA601.A1; also elsewhere on the board
/qs_Processors/DUE_LED_GREEN: XA601.D11; also elsewhere on the board
/qs_Processors/DUE_LED_RED: XA601.D10 (D10_CS0); also elsewhere on the board
/qs_Processors/DUE_PC_FAN: XA601.D7; also elsewhere on the board
/qs_Processors/DUE_PSON: XA601.D2; also elsewhere on the board
/qs_Processors/DUE_RESET: XA601.RST1 (RESET); also elsewhere on the board
/qs_Processors/ESP_CD: U601.29 (IO5); also elsewhere on the board
/qs_Processors/ESP_CLK: U601.12 (IO14); also elsewhere on the board
/qs_Processors/ESP_CMD: U601.23 (IO15); also elsewhere on the board
/qs_Processors/ESP_D0: U601.24 (IO2); also elsewhere on the board
/qs_Processors/ESP_D1: U601.26 (IO4); also elsewhere on the board
/qs_Processors/ESP_D2: U601.13 (IO12); also elsewhere on the board
/qs_Processors/ESP_D3: U601.15 (IO13); also elsewhere on the board
/qs_Processors/ESP_RX: U601.27 (IO16), XA601.D18 (D18_TX1)
/qs_Processors/ESP_SD_SEL: U601.25 (IO0); also elsewhere on the board
/qs_Processors/ESP_TX: U601.28 (IO17), XA601.D19 (D19_RX1)
/qs_Processors/FIL_RUNOUT: XA601.D45; also elsewhere on the board
/qs_Processors/X_STOP: XA601.D44; also elsewhere on the board
/qs_Processors/Y_STOP: XA601.D48; also elsewhere on the board
/qs_Processors/Z_STOP: XA601.D47; also elsewhere on the board
/qs_SD_Interface/DUE_CD: XA601.A3; also elsewhere on the board
/qs_SD_Interface/DUE_CS: XA601.A2; also elsewhere on the board
/qs_Temp_Control/BED_HEAT: XA601.D9; also elsewhere on the board
/qs_Temp_Control/BED_THERM: XA601.A0; also elsewhere on the board
GND: J601.4 (GND), J601.5 (Shield), J602.4 (GND), J602.5 (Shield), U601.14 (GND), U601.32 (GND), U601.38 (GND), XA601.GND2 (GND), XA601.GND3 (GND), XA601.GND5 (GND), XA601.GND6 (GND); also elsewhere on the board
unnamed: J601.1 (VBUS), J602.1 (VBUS)

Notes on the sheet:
Pulled up in a different schematic sheet
Routing Due USB connection to front
ESP32
IO0 controls BOOT Mode Fix in future rev
SCL1
DUE_SCL
10k
Arduino Due
Ran into issues with I2C clock stretching with Due TWI interface Fix with this circuit in future

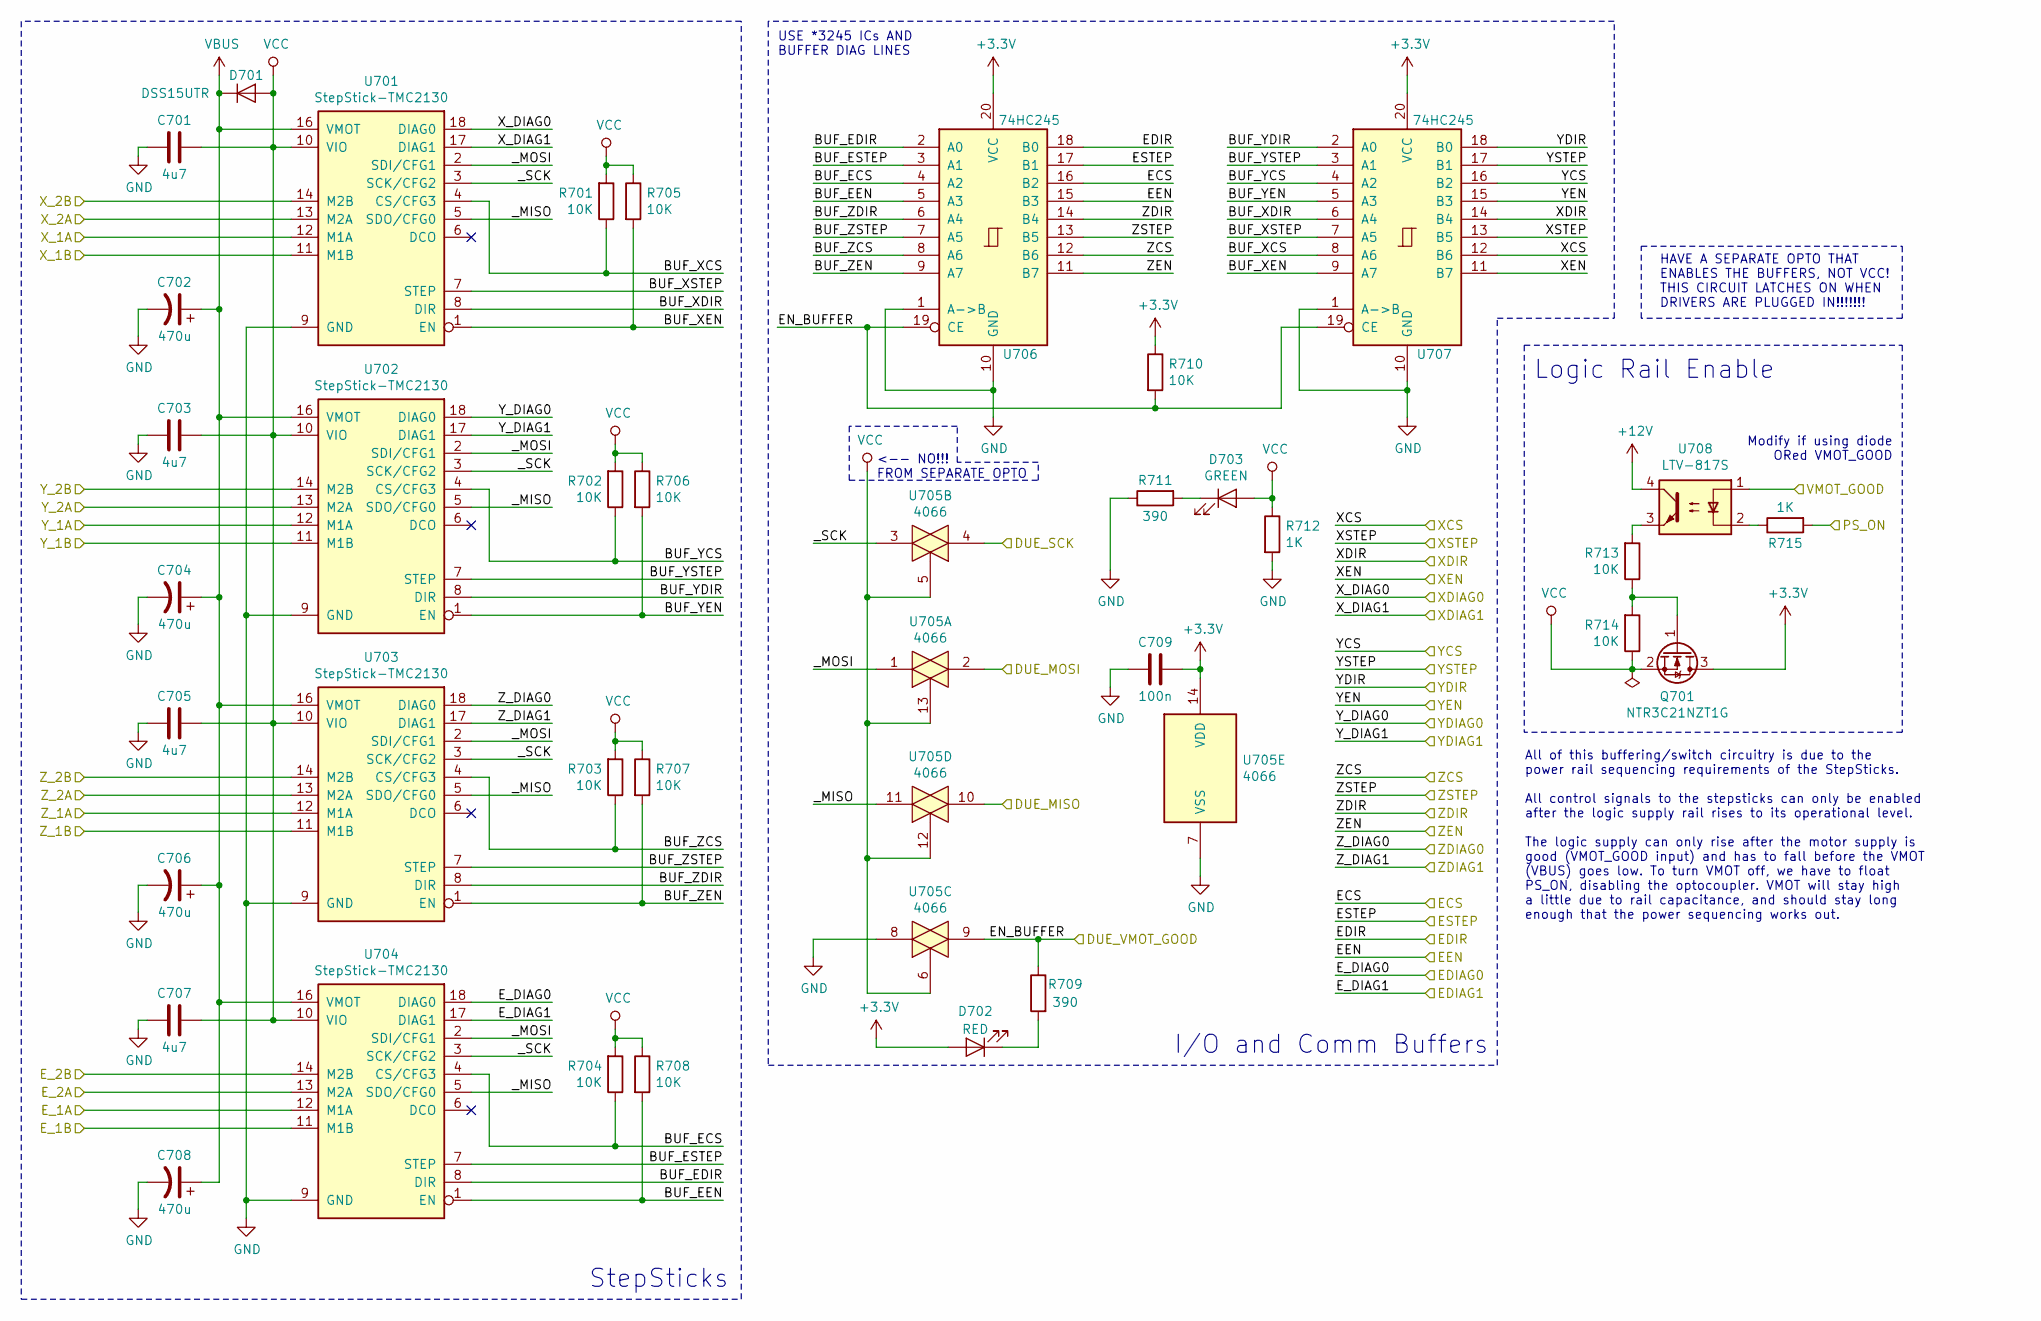
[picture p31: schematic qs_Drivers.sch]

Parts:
C701, C703, C705, C707: 4u7; C_0805_2012Metric_Pad1.15x1.40mm_HandSolder
C702, C704, C706, C708: 470u; CP_Radial_D12.5mm_P5.00mm; Part No. EEU-FM1H471
C709: 100n; C_0603_1608Metric_Pad1.05x0.95mm_HandSolder
D701: DSS15UTR; D_SOD-123F
D702: RED; LED_0603_1608Metric_Pad1.05x0.95mm_HandSolder
D703: GREEN; LED_0603_1608Metric_Pad1.05x0.95mm_HandSolder
Q701: NTR3C21NZT1G; SOT-23_Handsoldering
R701, R702, R703, R704, R705, R706, R707, R708, R710, R713, R714: 10K; R_0603_1608Metric_Pad1.05x0.95mm_HandSolder
R709, R711: 390; R_0603_1608Metric_Pad1.05x0.95mm_HandSolder
R712, R715: 1K; R_0603_1608Metric_Pad1.05x0.95mm_HandSolder
U701, U702, U703, U704: StepStick-TMC2130; TMC-21x0
U705: 4066; SSOP-14_5.3x6.2mm_P0.65mm
U706, U707: 74HC245; SSOP-20_5.3x7.2mm_P0.65mm; Part No. SN74HC245DBR
U708: LTV-817S; SMDIP-4_W9.53mm

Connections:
+3V3: C709.2, D702.2 (A), Q701.3 (D), R710.1, U705.14 (VDD), U706.20 (VCC), U707.20 (VCC); also elsewhere on the board
+12V: U708.4; also elsewhere on the board
/ATX_Connections/PS_ON: R715.2; also elsewhere on the board
/qs_Drivers/BUF_ECS: R704.1, U704.4 (CS/CFG3), U706.4 (A2)
/qs_Drivers/BUF_EDIR: U704.8 (DIR), U706.2 (A0)
/qs_Drivers/BUF_EEN: R708.2, U704.1 (EN), U706.5 (A3)
/qs_Drivers/BUF_ESTEP: U704.7 (STEP), U706.3 (A1)
/qs_Drivers/BUF_XCS: R701.1, U701.4 (CS/CFG3), U707.8 (A6)
/qs_Drivers/BUF_XDIR: U701.8 (DIR), U707.6 (A4)
/qs_Drivers/BUF_XEN: R705.2, U701.1 (EN), U707.9 (A7)
/qs_Drivers/BUF_XSTEP: U701.7 (STEP), U707.7 (A5)
/qs_Drivers/BUF_YCS: R702.1, U702.4 (CS/CFG3), U707.4 (A2)
/qs_Drivers/BUF_YDIR: U702.8 (DIR), U707.2 (A0)
/qs_Drivers/BUF_YEN: R706.2, U702.1 (EN), U707.5 (A3)
/qs_Drivers/BUF_YSTEP: U702.7 (STEP), U707.3 (A1)
/qs_Drivers/BUF_ZCS: R703.1, U703.4 (CS/CFG3), U706.8 (A6)
/qs_Drivers/BUF_ZDIR: U703.8 (DIR), U706.6 (A4)
/qs_Drivers/BUF_ZEN: R707.2, U703.1 (EN), U706.9 (A7)
/qs_Drivers/BUF_ZSTEP: U703.7 (STEP), U706.7 (A5)
/qs_Drivers/DUE_MISO: U705.10; also elsewhere on the board
/qs_Drivers/DUE_MOSI: U705.2; also elsewhere on the board
/qs_Drivers/DUE_SCK: U705.4; also elsewhere on the board
/qs_Drivers/DUE_VMOT_GOOD: R709.1, R710.2, U705.9, U706.19 (CE), U707.19 (CE); also elsewhere on the board
/qs_Drivers/ECS: U706.16 (B2); also elsewhere on the board
/qs_Drivers/EDIAG0: U704.18 (DIAG0); also elsewhere on the board
/qs_Drivers/EDIAG1: U704.17 (DIAG1); also elsewhere on the board
/qs_Drivers/EDIR: U706.18 (B0); also elsewhere on the board
/qs_Drivers/EEN: U706.15 (B3); also elsewhere on the board
/qs_Drivers/ESTEP: U706.17 (B1); also elsewhere on the board
/qs_Drivers/VMOT_GOOD: U708.1; also elsewhere on the board
/qs_Drivers/XCS: U707.12 (B6); also elsewhere on the board
/qs_Drivers/XDIAG0: U701.18 (DIAG0); also elsewhere on the board
/qs_Drivers/XDIAG1: U701.17 (DIAG1); also elsewhere on the board
/qs_Drivers/XDIR: U707.14 (B4); also elsewhere on the board
/qs_Drivers/XEN: U707.11 (B7); also elsewhere on the board
/qs_Drivers/XSTEP: U707.13 (B5); also elsewhere on the board
/qs_Drivers/X_1A: U701.12 (M1A); also elsewhere on the board
/qs_Drivers/X_1B: U701.11 (M1B); also elsewhere on the board
/qs_Drivers/X_2A: U701.13 (M2A); also elsewhere on the board
/qs_Drivers/X_2B: U701.14 (M2B); also elsewhere on the board
/qs_Drivers/YCS: U707.16 (B2); also elsewhere on the board
/qs_Drivers/YDIAG0: U702.18 (DIAG0); also elsewhere on the board
/qs_Drivers/YDIAG1: U702.17 (DIAG1); also elsewhere on the board
/qs_Drivers/YDIR: U707.18 (B0); also elsewhere on the board
/qs_Drivers/YEN: U707.15 (B3); also elsewhere on the board
/qs_Drivers/YSTEP: U707.17 (B1); also elsewhere on the board
/qs_Drivers/ZCS: U706.12 (B6); also elsewhere on the board
/qs_Drivers/ZDIAG0: U703.18 (DIAG0); also elsewhere on the board
/qs_Drivers/ZDIAG1: U703.17 (DIAG1); also elsewhere on the board
/qs_Drivers/ZDIR: U706.14 (B4); also elsewhere on the board
/qs_Drivers/ZEN: U706.11 (B7); also elsewhere on the board
/qs_Drivers/ZSTEP: U706.13 (B5); also elsewhere on the board
/qs_Drivers/_MISO: U701.5 (SDO/CFG0), U702.5 (SDO/CFG0), U703.5 (SDO/CFG0), U704.5 (SDO/CFG0), U705.11
/qs_Drivers/_MOSI: U701.2 (SDI/CFG1), U702.2 (SDI/CFG1), U703.2 (SDI/CFG1), U704.2 (SDI/CFG1), U705.1
/qs_Drivers/_SCK: U701.3 (SCK/CFG2), U702.3 (SCK/CFG2), U703.3 (SCK/CFG2), U704.3 (SCK/CFG2), U705.3
/qs_gantry_conn/EXT_1A: U704.12 (M1A); also elsewhere on the board
/qs_gantry_conn/EXT_1B: U704.11 (M1B); also elsewhere on the board
/qs_gantry_conn/EXT_2A: U704.13 (M2A); also elsewhere on the board
/qs_gantry_conn/EXT_2B: U704.14 (M2B); also elsewhere on the board
/qs_ymotor_fil/YMOT_1A: U702.12 (M1A); also elsewhere on the board
/qs_ymotor_fil/YMOT_1B: U702.11 (M1B); also elsewhere on the board
/qs_ymotor_fil/YMOT_2A: U702.13 (M2A); also elsewhere on the board
/qs_ymotor_fil/YMOT_2B: U702.14 (M2B); also elsewhere on the board
/qs_zmotor_stop/ZMOT_1A: U703.12 (M1A); also elsewhere on the board
/qs_zmotor_stop/ZMOT_1B: U703.11 (M1B); also elsewhere on the board
/qs_zmotor_stop/ZMOT_2A: U703.13 (M2A); also elsewhere on the board
/qs_zmotor_stop/ZMOT_2B: U703.14 (M2B); also elsewhere on the board
GND: C701.1, C702.2, C703.1, C704.2, C705.1, C706.2, C707.1, C708.2, C709.1, R711.1, R712.2, U701.9 (GND), U701.15 (GND), U702.9 (GND), U702.15 (GND), U703.9 (GND), U703.15 (GND), U704.9 (GND), U704.15 (GND), U705.7 (VSS), U705.8, U706.1 (A->B), U706.10 (GND), U707.1 (A->B), U707.10 (GND); also elsewhere on the board
unnamed: D702.1 (K), R709.2
unnamed: D703.1 (K), R711.2
unnamed: Q701.1 (G), R713.1, R714.2
unnamed: R713.2, U708.3
unnamed: R715.1, U708.2
VBUS: C702.1, C704.1, C706.1, C708.1, D701.1 (K), U701.16 (VMOT), U702.16 (VMOT), U703.16 (VMOT), U704.16 (VMOT); also elsewhere on the board
VCC: C701.2, C703.2, C705.2, C707.2, D701.2 (A), D703.2 (A), Q701.2 (S), R701.2, R702.2, R703.2, R704.2, R705.1, R706.1, R707.1, R708.1, R712.1, R714.1, U701.10 (VIO), U702.10 (VIO), U703.10 (VIO), U704.10 (VIO), U705.5, U705.6, U705.12, U705.13

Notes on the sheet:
StepSticks
I/O and Comm Buffers
Logic Rail Enable
All of this buffering/switch circuitry is due to the power rail sequencing requirements of the StepSticks. All control signals to the stepsticks can only be enabled after the logic supply rail rises to its operational level. The logic supply can only rise after the motor supply is good (VMOT_GOOD i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
HAVE A SEPARATE OPTO THAT ENABLES THE BUFFERS, NOT VCC! THIS CIRCUIT LATCHES ON WHEN DRIVERS ARE PLUGGED IN!!!!!!!
<-- NO!!! FROM SEPARATE OPTO
USE *3245 ICs AND BUFFER DIAG LINES
Modify if using diode ORed VMOT_GOOD

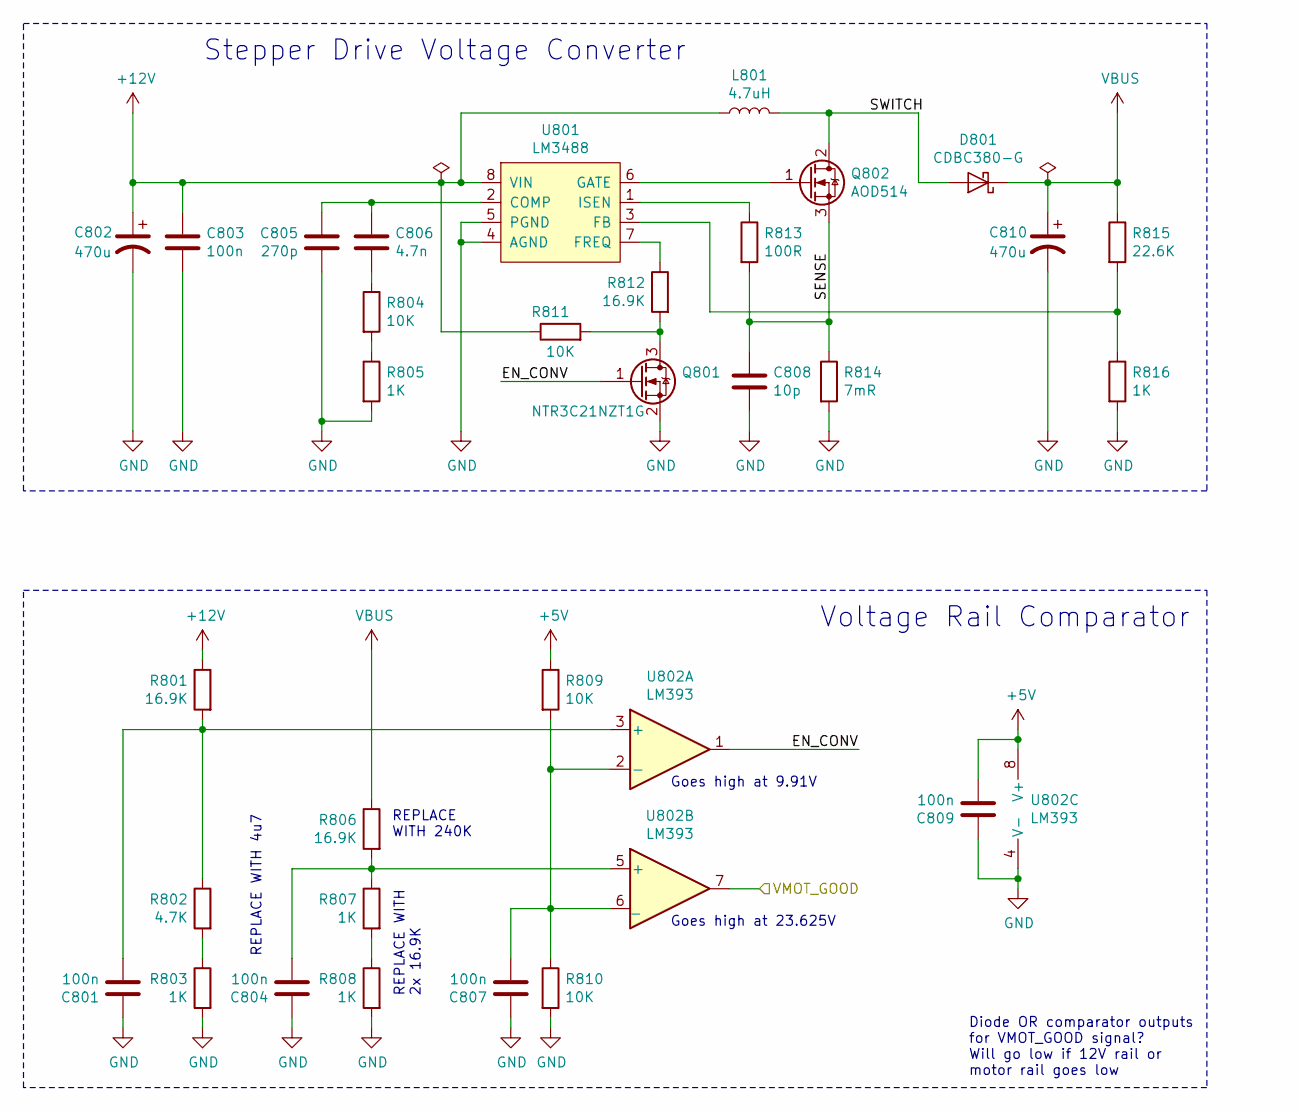
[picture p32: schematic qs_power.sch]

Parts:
C801, C803, C804, C807, C809: 100n; C_0603_1608Metric_Pad1.05x0.95mm_HandSolder
C802, C810: 470u; CP_Radial_D12.5mm_P5.00mm; Part No. EEU-FM1H471
C805: 270p; C_0603_1608Metric_Pad1.05x0.95mm_HandSolder
C806: 4.7n; C_0603_1608Metric_Pad1.05x0.95mm_HandSolder
C808: 10p; C_0603_1608Metric_Pad1.05x0.95mm_HandSolder
D801: CDBC380-G; D_SMC_Handsoldering
L801: 4.7uH; L_Bourns_SRR1260; Part No. SRR1260-4R7Y
Q801: NTR3C21NZT1G; SOT-23_Handsoldering
Q802: AOD514; TO-252-2
R801, R806, R812: 16.9K; R_0603_1608Metric_Pad1.05x0.95mm_HandSolder
R802: 4.7K; R_0603_1608Metric_Pad1.05x0.95mm_HandSolder
R803, R805, R807, R808, R816: 1K; R_0603_1608Metric_Pad1.05x0.95mm_HandSolder
R804, R809, R810, R811: 10K; R_0603_1608Metric_Pad1.05x0.95mm_HandSolder
R813: 100R; R_0603_1608Metric_Pad1.05x0.95mm_HandSolder
R814: 7mR; R_2512_6332Metric_Pad1.52x3.35mm_HandSolder; Part No. PE2512FKE7W0R007L
R815: 22.6K; R_0603_1608Metric_Pad1.05x0.95mm_HandSolder
U801: LM3488; VSSOP-8_3.0x3.0mm_P0.65mm
U802: LM393; MSOP-8_3x3mm_P0.65mm; Part No. TLV7032DGKR

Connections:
+5V: C809.2, R809.1, U802.8 (V+); also elsewhere on the board
+12V: C802.1, C803.1, L801.1, R801.1, R811.1, U801.8 (VIN); also elsewhere on the board
/qs_Drivers/VMOT_GOOD: U802.7; also elsewhere on the board
/qs_power/EN_CONV: Q801.1 (G), U802.1
/qs_power/SENSE: C808.1, Q802.3 (S), R813.2, R814.1
/qs_power/SWITCH: D801.2 (A), L801.2, Q802.2 (D)
GND: C801.1, C802.2, C803.2, C804.1, C805.1, C807.1, C808.2, C809.1, C810.2, Q801.2 (S), R803.2, R805.2, R808.2, R810.2, R814.2, R816.2, U801.4 (AGND), U801.5 (PGND), U802.4 (V-); also elsewhere on the board
unnamed: C801.2, R801.2, R802.1, U802.3 (+)
unnamed: C804.2, R806.2, R807.1, U802.5 (+)
unnamed: C805.2, C806.1, U801.2 (COMP)
unnamed: C806.2, R804.1
unnamed: C807.2, R809.2, R810.1, U802.2 (-), U802.6 (_)
unnamed: Q801.3 (D), R811.2, R812.2
unnamed: Q802.1 (G), U801.6 (GATE)
unnamed: R802.2, R803.1
unnamed: R804.2, R805.1
unnamed: R807.2, R808.1
unnamed: R812.1, U801.7 (FREQ)
unnamed: R813.1, U801.1 (ISEN)
unnamed: R815.2, R816.1, U801.3 (FB)
VBUS: C810.1, D801.1 (K), R806.1, R815.1; also elsewhere on the board

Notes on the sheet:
Goes high at 23.625V
Goes high at 9.91V
Stepper Drive Voltage Converter
Voltage Rail Comparator
REPLACE WITH 240K
REPLACE WITH 2x 16.9K
REPLACE WITH 4u7
Diode OR comparator outputs for VMOT_GOOD signal? Will go low if 12V rail or motor rail goes low

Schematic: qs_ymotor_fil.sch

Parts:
D901, D902, D903, D904, D905, D906, D907, D908: DSS15UTR; D_SOD-123F
J901: Conn_02x03_Odd_Even; IDC-Header_2x03_P2.54mm_Vertical

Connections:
/FIL_SEN+: J901.4; also elsewhere on the board
/qs_ymotor_fil/YMOT_1A: D905.2 (A), D906.1 (K), J901.2; also elsewhere on the board
/qs_ymotor_fil/YMOT_1B: D901.2 (A), D902.1 (K), J901.1; also elsewhere on the board
/qs_ymotor_fil/YMOT_2A: D907.2 (A), D908.1 (K), J901.6; also elsewhere on the board
/qs_ymotor_fil/YMOT_2B: D903.2 (A), D904.1 (K), J901.5; also elsewhere on the board
GND: D902.2 (A), D904.2 (A), D906.2 (A), D908.2 (A), J901.3; also elsewhere on the board
VBUS: D901.1 (K), D903.1 (K), D905.1 (K), D907.1 (K); also elsewhere on the board

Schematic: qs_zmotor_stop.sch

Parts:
D1001, D1002, D1003, D1004, D1005, D1006, D1007, D1008: DSS15UTR; D_SOD-123F
J1001: Conn_02x03_Odd_Even; IDC-Header_2x03_P2.54mm_Vertical

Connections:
/Z_STOP+: J1001.4; also elsewhere on the board
/qs_zmotor_stop/ZMOT_1A: D1005.2 (A), D1006.1 (K), J1001.2; also elsewhere on the board
/qs_zmotor_stop/ZMOT_1B: D1001.2 (A), D1002.1 (K), J1001.1; also elsewhere on the board
/qs_zmotor_stop/ZMOT_2A: D1007.2 (A), D1008.1 (K), J1001.6; also elsewhere on the board
/qs_zmotor_stop/ZMOT_2B: D1003.2 (A), D1004.1 (K), J1001.5; also elsewhere on the board
GND: D1002.2 (A), D1004.2 (A), D1006.2 (A), D1008.2 (A), J1001.3; also elsewhere on the board
VBUS: D1001.1 (K), D1003.1 (K), D1005.1 (K), D1007.1 (K); also elsewhere on the board

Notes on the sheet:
Using diode bridges instead instead of discrete diodes for cost and space reasons

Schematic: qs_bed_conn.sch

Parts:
J1101: Conn_02x13_Odd_Even; IDC-Header_2x13_P2.54mm_Vertical

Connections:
/qs_bed_conn/BED-: J1101.3, J1101.5, J1101.7, J1101.9, J1101.11, J1101.13, J1101.15, J1101.17, J1101.19, J1101.21, J1101.23, J1101.25; also elsewhere on the board
/qs_bed_conn/THERM+: J1101.1; also elsewhere on the board
GND: J1101.2; also elsewhere on the board
VPP: J1101.4, J1101.6, J1101.8, J1101.10, J1101.12, J1101.14, J1101.16, J1101.18, J1101.20, J1101.22, J1101.24, J1101.26; also elsewhere on the board

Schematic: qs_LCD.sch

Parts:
C1201, C1202: 100n; C_0603_1608Metric_Pad1.05x0.95mm_HandSolder
D1201, D1202: 3.6V; D_SOD-323_HandSoldering; Part No. MM3Z3V6T1G
J1201: Conn_02x05_Odd_Even; IDC-Header_2x05_P2.54mm_Vertical
R1201, R1202: 10K; R_0603_1608Metric_Pad1.05x0.95mm_HandSolder
U401: 74HC14; TSSOP-14_4.4x5mm_P0.65mm

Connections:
+5V: J1201.10; also elsewhere on the board
/ENC_A: U401.6; also elsewhere on the board
/ENC_B: U401.4; also elsewhere on the board
/qs_I2C_LEDs/B_DRAIN: J1201.8; also elsewhere on the board
/qs_I2C_LEDs/G_DRAIN: J1201.6; also elsewhere on the board
/qs_I2C_LEDs/LCL: J1201.7; also elsewhere on the board
/qs_I2C_LEDs/LDA: J1201.9; also elsewhere on the board
/qs_LCD/LED_RED: J1201.4; also elsewhere on the board
GND: C1201.2, C1202.2, D1201.2 (A), D1202.2 (A), J1201.2; also elsewhere on the board
unnamed: C1201.1, D1201.1 (K), R1201.2, U401.3
unnamed: C1202.1, D1202.1 (K), R1202.2, U401.5
unnamed: J1201.3, R1201.1
unnamed: J1201.5, R1202.1

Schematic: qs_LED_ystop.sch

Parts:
J1301: Conn_02x03_Odd_Even; IDC-Header_2x03_P2.54mm_Vertical

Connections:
+12V: J1301.3; also elsewhere on the board
/Y_STOP+: J1301.5; also elsewhere on the board
/qs_I2C_LEDs/B_DRAIN: J1301.1; also elsewhere on the board
/qs_I2C_LEDs/G_DRAIN: J1301.2; also elsewhere on the board
/qs_LCD/LED_RED: J1301.4; also elsewhere on the board
GND: J1301.6; also elsewhere on the board

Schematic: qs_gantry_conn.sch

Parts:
D1401, D1402, D1403, D1404, D1405, D1406, D1407, D1408, D1409, D1410, D1411, D1412, D1413, D1414, D1415, D1416: DSS15UTR; D_SOD-123F
J1401: Conn_02x10_Odd_Even; IDC-Header_2x10_P2.54mm_Vertical

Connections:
+12V: J1401.5, J1401.7, J1401.9; also elsewhere on the board
/EXT-: J1401.11, J1401.13, J1401.15; also elsewhere on the board
/PRINT_FAN-: J1401.6; also elsewhere on the board
/THERM+: J1401.10; also elsewhere on the board
/X_STOP+: J1401.14; also elsewhere on the board
/qs_Drivers/X_1A: D1403.2 (A), D1404.1 (K), J1401.19; also elsewhere on the board
/qs_Drivers/X_1B: D1407.2 (A), D1408.1 (K), J1401.17; also elsewhere on the board
/qs_Drivers/X_2A: D1415.2 (A), D1416.1 (K), J1401.20; also elsewhere on the board
/qs_Drivers/X_2B: D1411.2 (A), D1412.1 (K), J1401.18; also elsewhere on the board
/qs_gantry_conn/EXT_1A: D1413.2 (A), D1414.1 (K), J1401.2; also elsewhere on the board
/qs_gantry_conn/EXT_1B: D1409.2 (A), D1410.1 (K), J1401.4; also elsewhere on the board
/qs_gantry_conn/EXT_2A: D1401.2 (A), D1402.1 (K), J1401.1; also elsewhere on the board
/qs_gantry_conn/EXT_2B: D1405.2 (A), D1406.1 (K), J1401.3; also elsewhere on the board
GND: D1402.2 (A), D1404.2 (A), D1406.2 (A), D1408.2 (A), D1410.2 (A), D1412.2 (A), D1414.2 (A), D1416.2 (A), J1401.8, J1401.12, J1401.16; also elsewhere on the board
VBUS: D1401.1 (K), D1403.1 (K), D1405.1 (K), D1407.1 (K), D1409.1 (K), D1411.1 (K), D1413.1 (K), D1415.1 (K); also elsewhere on the board

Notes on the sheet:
Hotend Fan
Using diode bridges instead instead of discrete diodes for cost and space reasons

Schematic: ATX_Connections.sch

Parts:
F1501: 10A; Keystone_3557
F1502: 25A; Keystone_3557
J1501: Conn_01x02; JST_XH_B2B-XH-A_1x02_P2.50mm_Vertical
J1502: Conn_01x04; JST_XH_B4B-XH-A_1x04_P2.50mm_Vertical
J1503: Conn_XT; XT60-Male

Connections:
+5V: J1501.2; also elsewhere on the board
+12V: F1501.1, J1502.1, J1502.3; also elsewhere on the board
/ATX_Connections/LINE_IN: F1501.2, F1502.2, J1503.+
/ATX_Connections/PS_ON: J1501.1; also elsewhere on the board
GND: J1502.2, J1502.4, J1503.-; also elsewhere on the board
VPP: F1502.1; also elsewhere on the board

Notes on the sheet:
Heated Bed Supply



Board: 2 copper layers, 192.5 x 165.0 mm, 252 parts (8 on the bottom side), 188 nets.

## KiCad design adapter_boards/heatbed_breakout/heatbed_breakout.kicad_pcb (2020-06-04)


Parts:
D1: RED; LED_0603_1608Metric_Pad1.05x0.95mm_HandSolder
H1, H2: MountingHole; MountingHole_5.3mm_M5_Pad
J1: Conn_02x13_Odd_Even; IDC-Header_2x13_P2.54mm_Vertical
J2: Conn_XT; XT60-Female
J3: Conn_01x02; JST_XH_B2B-XH-A_1x02_P2.50mm_Vertical
R1: 2K; R_0603_1608Metric_Pad1.05x0.95mm_HandSolder

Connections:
/H+: J1.4, J1.6, J1.8, J1.10, J1.12, J1.14, J1.16, J1.18, J1.20, J1.22, J1.24, J1.26, J2.+, R1.1
/H-: D1.1 (K), J1.3, J1.5, J1.7, J1.9, J1.11, J1.13, J1.15, J1.17, J1.19, J1.21, J1.23, J1.25, J2.-
unnamed: D1.2 (A), R1.2
unnamed: J1.1, J3.1
unnamed: J1.2, J3.2

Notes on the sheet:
M5 Mounting Holes


Board: 2 copper layers, 85.0 x 28.0 mm, 7 parts (0 on the bottom side), 5 nets.

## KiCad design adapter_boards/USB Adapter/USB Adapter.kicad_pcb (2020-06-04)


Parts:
J101: USB_A; USB_A_CNC_Tech-1001-008B-01001
J102, J103: Conn_01x02; PinHeader_1x02_P2.54mm_Vertical
J104: Conn_01x04; PinHeader_1x04_P2.54mm_Vertical

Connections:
/D+: J101.3 (D+), J104.2
/D-: J101.2 (D-), J104.3
/VBUS: J101.1 (VBUS), J104.4
GND: J101.4 (GND), J104.1
unnamed: J101.5 (Shield), J102.1, J102.2, J103.1, J103.2



Board: 2 copper layers, 17.8 x 10.2 mm, 4 parts (3 on the bottom side), 5 nets.

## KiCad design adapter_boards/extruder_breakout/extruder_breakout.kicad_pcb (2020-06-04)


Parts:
D1, D2, D3: RED; LED_0603_1608Metric_Pad1.05x0.95mm_HandSolder
H1, H2: MountingHole; MountingHole_3.2mm_M3_Pad
J1: Conn_XT; XT30U-F
J2: Conn_02x08_Odd_Even; IDC-Header_2x08_P2.54mm_Vertical
J3: Screw_Terminal_01x02; TerminalBlock_TE_2.54mmx02
J4: Conn_01x04; JST_XH_B4B-XH-A_1x04_P2.50mm_Vertical
J5, J6, J7: Conn_01x02; JST_XH_B2B-XH-A_1x02_P2.50mm_Vertical
R1, R2, R3: 2K; R_0603_1608Metric_Pad1.05x0.95mm_HandSolder

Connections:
+12V: J1.+, J2.11, J2.13, J2.15, J6.1, J7.1, R1.2, R2.2, R3.2
/EXT_1A: J2.2, J4.3
/EXT_1B: J2.4, J4.4
/EXT_2A: J2.1, J4.2
/EXT_2B: J2.3, J4.1
/Endstop_A: J2.14, J5.1
/Endstop_B: J2.16, J5.2
/H-: D3.1 (K), J1.-, J2.5, J2.7, J2.9
/HFan-: D1.1 (K), J2.8, J7.2
/Print_Fan-: D2.1 (K), J2.6, J6.2
/Therm_A: J2.10, J3.2
/Therm_B: J2.12, J3.1
unnamed: D1.2 (A), R1.1
unnamed: D2.2 (A), R2.1
unnamed: D3.2 (A), R3.1

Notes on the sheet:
Print Fan
Hotend Fan
Heater
Endstop
Extruder Stepper
Thermistor
M3 Mounting Holes


Board: 2 copper layers, 29.0 x 50.0 mm, 15 parts (0 on the bottom side), 15 nets.

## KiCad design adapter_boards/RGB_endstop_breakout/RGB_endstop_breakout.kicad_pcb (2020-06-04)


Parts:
H1, H2: MountingHole; MountingHole_5.3mm_M5_Pad
J1: Conn_02x03_Odd_Even; IDC-Header_2x03_P2.54mm_Vertical
J2, J3: Conn_01x04; JST_XH_B4B-XH-A_1x04_P2.50mm_Vertical
J4: Conn_01x02; JST_XH_B2B-XH-A_1x02_P2.50mm_Vertical

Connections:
/12V: J1.3, J2.1, J3.1
/BLUE: J1.1, J2.4, J3.4
/GREEN: J1.2, J2.2, J3.2
/RED: J1.4, J2.3, J3.3
unnamed: J1.5, J4.2
unnamed: J1.6, J4.1

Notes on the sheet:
M5 Mounting Holes


Board: 2 copper layers, 40.0 x 35.0 mm, 6 parts (0 on the bottom side), 6 nets.

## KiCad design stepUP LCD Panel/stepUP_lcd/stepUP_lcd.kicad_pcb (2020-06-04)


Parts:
BZ1: Buzzer; Buzzer_CUI_CPT9019S
C2, C3: 100n; C_0603_1608Metric_Pad1.05x0.95mm_HandSolder
D1, D2, D3: LED; LED_1206ReverseMount
G101: Stepper Icon; Icon_Stepper
G102: SD Icon; Icon_SD
G103: Hot Icon; Icon_Temp
H1: MountingHole; RGB_Encoder_Hole
H2, H3, H4, H5, H6: MountingHole; MountingHole_5.3mm_M5_Pad
H7, H8, H9, H10, H11, H12, H13, H14, H15: MountingHole; MountingHole_3.2mm_M3_Pad
J1: Conn_02x05_Odd_Even; PinHeader_2x05_P2.54mm_Shrouded
J2: Conn_02x04_Odd_Even; PinHeader_2x04_P2.54mm_Vertical_SMD
J3: Conn_01x18; PinHeader_1x18_P2.54mm_Vertical_SMD_Pin1Left
R1, R3: 4K7; R_0603_1608Metric_Pad1.05x0.95mm_HandSolder
R2: 10K; R_0603_1608Metric_Pad1.05x0.95mm_HandSolder
R4, R5, R6: 0R; R_0603_1608Metric_Pad1.05x0.95mm_HandSolder
R7, R8, R9, R10, R11, R12: 390R; R_0603_1608Metric_Pad1.05x0.95mm_HandSolder
R101, R102: 1K; R_0603_1608Metric_Pad1.05x0.95mm_HandSolder
RV1: R_POT; Potentiometer_Vishay_TS53YJ
U2: P82B715; SOIC-8_3.9x4.9mm_P1.27mm
U3: MCP23017_SS; SSOP-28_5.3x10.2mm_P0.65mm

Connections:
+5V: C2.2, C3.2, J1.10, J2.2, J3.4, J3.17, R1.2, R2.2, R3.1, R10.1, R11.1, R12.1, R101.2, R102.2, RV1.1, U2.8 (VCC), U3.9 (VDD)
/BLUE: J1.8, R6.1, R9.1
/BUZZ: BZ1.1 (-), U3.26 (GPA5)
/D4: J3.8, U3.5 (GPB4)
/D5: J3.7, U3.4 (GPB3)
/D6: J3.6, U3.3 (GPB2)
/D7: J3.5, U3.2 (GPB1)
/E: J3.13, U3.6 (GPB5)
/EN_A: J1.3, J2.6, R101.1, U3.21 (GPA0)
/EN_B: J1.5, J2.4, R102.1, U3.22 (GPA1)
/EN_BLUE: J2.3, R9.2
/EN_C: J2.8, U3.23 (GPA2)
/EN_GREEN: J2.5, R8.2
/EN_RED: J2.7, R7.2
/GREEN: J1.6, R5.1, R8.1
/LCD_BLUE: J3.1, R6.2
/LCD_GREEN: J3.2, R5.2
/LCD_RED: J3.3, R4.2
/LCL: J1.7, U2.7 (LCL)
/LDA: J1.9, U2.2 (LDA)
/LED1: D1.1 (K), U3.1 (GPB0)
/LED2: D2.1 (K), U3.28 (GPA7)
/LED3: D3.1 (K), U3.27 (GPA6)
/RED: J1.4, R4.1, R7.1
/RS: J3.15, U3.8 (GPB7)
/RW: J3.14, U3.7 (GPB6)
GND: BZ1.2 (+), C2.1, C3.1, J1.2, J2.1, J3.18, RV1.3, U2.4 (GND), U3.10 (VSS), U3.15 (A0), U3.16 (A1), U3.17 (A2)
unnamed: D1.2 (A), R10.2
unnamed: D2.2 (A), R11.2
unnamed: D3.2 (A), R12.2
unnamed: J3.16, RV1.2
unnamed: R1.1, U2.3 (SDA), U3.13 (SDA)
unnamed: R2.1, U3.18 (~RESET~)
unnamed: R3.2, U2.6 (SCL), U3.12 (SCK)

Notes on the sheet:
Encoder Daughterboard PINS ARE MIRRORED
RGB LCD Connection PINS ARE MIRRORED FOR REVERSE MOUNT
M5 Mounting Holes
M3 Mounting Holes



Board: 2 copper layers, 180.0 x 90.0 mm, 44 parts (26 on the bottom side), 34 nets.

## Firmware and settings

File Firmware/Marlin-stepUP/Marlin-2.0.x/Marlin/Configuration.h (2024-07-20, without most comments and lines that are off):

#pragma once
#define CONFIGURATION_H_VERSION 020005
#define STRING_CONFIG_H_AUTHOR "Ishaan Govindarajan" // Who made the changes.
#define SHOW_BOOTSCREEN
#define SERIAL_PORT 0
#define SERIAL_PORT_2 1
#define BAUDRATE 250000
  #define MOTHERBOARD BOARD_QUICKSTEP
#define CUSTOM_MACHINE_NAME "stepUP"
#define EXTRUDERS 1
#define DEFAULT_NOMINAL_FILAMENT_DIA 1.75
#define PSU_CONTROL
  #define PSU_ACTIVE_HIGH true     // Set 'false' for ATX, 'true' for X-Box
  #define PSU_DEFAULT_OFF         // Keep power off until enabled directly with M80
  #define PSU_POWERUP_DELAY 250   // (ms) Delay for the PSU to warm up to full power
  #define AUTO_POWER_CONTROL      // Enable automatic control of the PS_ON pin
    #define AUTO_POWER_FANS         // Turn on PSU if fans need power
    #define AUTO_POWER_E_TEMP        65 // (°C) Turn on PSU over this temperature
#define TEMP_SENSOR_0 5
#define TEMP_SENSOR_1 0
#define TEMP_SENSOR_2 0
#define TEMP_SENSOR_3 0
#define TEMP_SENSOR_4 0
#define TEMP_SENSOR_5 0
#define TEMP_SENSOR_6 0
#define TEMP_SENSOR_7 0
#define TEMP_SENSOR_BED 11
#define TEMP_SENSOR_PROBE 0
#define TEMP_SENSOR_CHAMBER 0
#define DUMMY_THERMISTOR_998_VALUE 25
#define DUMMY_THERMISTOR_999_VALUE 100
#define MAX_REDUNDANT_TEMP_SENSOR_DIFF 10
#define TEMP_RESIDENCY_TIME     10  // (seconds) Time to wait for hotend to "settle" in M109
#define TEMP_WINDOW              1  // (°C) Temperature proximity for the "temperature reached" timer
#define TEMP_HYSTERESIS          3  // (°C) Temperature proximity considered "close enough" to the target
#define TEMP_BED_RESIDENCY_TIME 10  // (seconds) Time to wait for bed to "settle" in M190
#define TEMP_BED_WINDOW          1  // (°C) Temperature proximity for the "temperature reached" timer
#define TEMP_BED_HYSTERESIS      3  // (°C) Temperature proximity considered "close enough" to the target
#define HEATER_0_MINTEMP   5
#define HEATER_1_MINTEMP   5
#define HEATER_2_MINTEMP   5
#define HEATER_3_MINTEMP   5
#define HEATER_4_MINTEMP   5
#define HEATER_5_MINTEMP   5
#define HEATER_6_MINTEMP   5
#define HEATER_7_MINTEMP   5
#define BED_MINTEMP        5
#define HEATER_0_MAXTEMP 300
#define HEATER_1_MAXTEMP 275
#define HEATER_2_MAXTEMP 275
#define HEATER_3_MAXTEMP 275
#define HEATER_4_MAXTEMP 275
#define HEATER_5_MAXTEMP 275
#define HEATER_6_MAXTEMP 275
#define HEATER_7_MAXTEMP 275
#define BED_MAXTEMP      125
#define PIDTEMP
#define BANG_MAX 255     // Limits current to nozzle while in bang-bang mode; 255=full current
#define PID_MAX BANG_MAX // Limits current to nozzle while PID is active (see PID_FUNCTIONAL_RANGE below); 255=full current
#define PID_K1 0.95      // Smoothing factor within any PID loop
  #define PID_AUTOTUNE_MENU     // Add PID -tuning to the "Advanced Settings" menu. (~250 bytes of PROGMEM)
  #define SLOW_PWM_HEATERS      // PWM with very low frequency (roughly 0.125Hz=8s) and minimum state time of approximately 1s useful for heaters driven by a relay
  #define PID_FUNCTIONAL_RANGE 10 // If the temperature difference between the target temperature and the actual temperature
  #define DEFAULT_Kp 17.39
  #define DEFAULT_Ki 1.04
  #define DEFAULT_Kd 73.05
#define PIDTEMPBED
#define MAX_BED_POWER 255 // limits duty cycle to bed; 255=full current
  #define DEFAULT_bedKp 49.67
  #define DEFAULT_bedKi 4.03
  #define DEFAULT_bedKd 407.98
#define PREVENT_COLD_EXTRUSION
#define EXTRUDE_MINTEMP 160
#define PREVENT_LENGTHY_EXTRUDE
#define EXTRUDE_MAXLENGTH 200
#define THERMAL_PROTECTION_HOTENDS // Enable thermal protection for all extruders
#define THERMAL_PROTECTION_BED     // Enable thermal protection for the heated bed
#define USE_YMIN_PLUG
#define USE_XMAX_PLUG
#define USE_ZMAX_PLUG
#define X_MIN_ENDSTOP_INVERTING false // Set to true to invert the logic of the endstop.
#define Y_MIN_ENDSTOP_INVERTING false // Set to true to invert the logic of the endstop.
#define Z_MIN_ENDSTOP_INVERTING false // Set to true to invert the logic of the endstop.
#define X_MAX_ENDSTOP_INVERTING false // Set to true to invert the logic of the endstop.
#define Y_MAX_ENDSTOP_INVERTING false // Set to true to invert the logic of the endstop.
#define Z_MAX_ENDSTOP_INVERTING false // Set to true to invert the logic of the endstop.
#define Z_MIN_PROBE_ENDSTOP_INVERTING false // Set to true to invert the logic of the probe.
#define X_DRIVER_TYPE  TMC2130
#define Y_DRIVER_TYPE  TMC2130
#define Z_DRIVER_TYPE  TMC2130
#define E0_DRIVER_TYPE TMC2130
#define ENDSTOP_INTERRUPTS_FEATURE
#define DEFAULT_AXIS_STEPS_PER_UNIT   { 100, 100, 400, 407 }
#define DEFAULT_MAX_FEEDRATE          { 200, 200, 40, 50 }
#define DEFAULT_MAX_ACCELERATION      { 1000, 650, 100, 7500 }
#define DEFAULT_ACCELERATION          3000    // X, Y, Z and E acceleration for printing moves
#define DEFAULT_RETRACT_ACCELERATION  10000    // E acceleration for retracts
#define DEFAULT_TRAVEL_ACCELERATION   3000    // X, Y, Z acceleration for travel (non printing) moves
#define CLASSIC_JERK
  #define DEFAULT_XJERK 2.5
  #define DEFAULT_YJERK 2.5
  #define DEFAULT_ZJERK  1
  #define LIMITED_JERK_EDITING        // Limit edit via M205 or LCD to DEFAULT_aJERK * 2
    #define MAX_JERK_EDIT_VALUES { 10, 10, 5, 10 } // ...or, set your own edit limits
#define DEFAULT_EJERK    2.5  // May be used by Linear Advance
#define S_CURVE_ACCELERATION
#define PROBE_MANUALLY
#define MANUAL_PROBE_START_Z 0.2
#define NOZZLE_TO_PROBE_OFFSET { 10, 10, 0 }
#define MIN_PROBE_EDGE 10
#define XY_PROBE_SPEED 8000
#define Z_PROBE_SPEED_FAST HOMING_FEEDRATE_Z
#define Z_PROBE_SPEED_SLOW (Z_PROBE_SPEED_FAST / 2)
#define Z_CLEARANCE_DEPLOY_PROBE   10 // Z Clearance for Deploy/Stow
#define Z_CLEARANCE_BETWEEN_PROBES  5 // Z Clearance between probe points
#define Z_CLEARANCE_MULTI_PROBE     5 // Z Clearance between multiple probes
#define Z_PROBE_LOW_POINT          -2 // Farthest distance below the trigger-point to go before stopping
#define Z_PROBE_OFFSET_RANGE_MIN -20
#define Z_PROBE_OFFSET_RANGE_MAX 20
#define X_ENABLE_ON 0
#define Y_ENABLE_ON 0
#define Z_ENABLE_ON 0
#define E_ENABLE_ON 0 // For all extruders
#define DISABLE_X false
#define DISABLE_Y false
#define DISABLE_Z false
#define DISABLE_E false             // For all extruders
#define DISABLE_INACTIVE_EXTRUDER   // Keep only the active extruder enabled
#define INVERT_X_DIR false
#define INVERT_Y_DIR false
#define INVERT_Z_DIR false
#define INVERT_E0_DIR true
#define INVERT_E1_DIR false
#define INVERT_E2_DIR false
#define INVERT_E3_DIR false
#define INVERT_E4_DIR false
#define INVERT_E5_DIR false
#define INVERT_E6_DIR false
#define INVERT_E7_DIR false
#define X_HOME_DIR 1
#define Y_HOME_DIR -1
#define Z_HOME_DIR 1
#define X_BED_SIZE 200
#define Y_BED_SIZE 220
#define X_MIN_POS -11.5
#define Y_MIN_POS -22
#define Z_MIN_POS 0
#define X_MAX_POS 216.5
#define Y_MAX_POS 215
#define Z_MAX_POS 212.5
#define MIN_SOFTWARE_ENDSTOPS
  #define MIN_SOFTWARE_ENDSTOP_X
  #define MIN_SOFTWARE_ENDSTOP_Y
  #define MIN_SOFTWARE_ENDSTOP_Z
#define MAX_SOFTWARE_ENDSTOPS
  #define MAX_SOFTWARE_ENDSTOP_X
  #define MAX_SOFTWARE_ENDSTOP_Y
  #define MAX_SOFTWARE_ENDSTOP_Z
#define FILAMENT_RUNOUT_SENSOR
  #define NUM_RUNOUT_SENSORS   1     // Number of sensors, up to one per extruder. Define a FIL_RUNOUT#_PIN for each.
  #define FIL_RUNOUT_INVERTING false // Set to true to invert the logic of the sensor.
  #define FILAMENT_RUNOUT_SCRIPT "M600"
  #define FILAMENT_RUNOUT_DISTANCE_MM 450
#define HOMING_FEEDRATE_XY (50*60)
#define HOMING_FEEDRATE_Z  (25*60)
#define VALIDATE_HOMING_ENDSTOPS
#define EEPROM_SETTINGS     // Persistent storage with M500 and M501
#define EEPROM_CHITCHAT       // Give feedback on EEPROM commands. Disable to save PROGMEM.
#define EEPROM_BOOT_SILENT    // Keep M503 quiet and only give errors during first load
#define HOST_KEEPALIVE_FEATURE        // Disable this if your host doesn't like keepalive messages
#define DEFAULT_KEEPALIVE_INTERVAL 2  // Number of seconds between "busy" messages. Set with M113.
#define BUSY_WHILE_HEATING            // Some hosts require "busy" messages even during heating
#define PREHEAT_1_LABEL       "PLA"
#define PREHEAT_1_TEMP_HOTEND 220
#define PREHEAT_1_TEMP_BED     65
#define PREHEAT_1_FAN_SPEED     0 // Value from 0 to 255
#define PREHEAT_2_LABEL       "PETG"
#define PREHEAT_2_TEMP_HOTEND 260
#define PREHEAT_2_TEMP_BED    75
#define PREHEAT_2_FAN_SPEED     0 // Value from 0 to 255
#define NOZZLE_PARK_FEATURE
  #define NOZZLE_PARK_POINT {200, -22, 20 }
  #define NOZZLE_PARK_XY_FEEDRATE 100   // (mm/s) X and Y axes feedrate (also used for delta Z axis)
  #define NOZZLE_PARK_Z_FEEDRATE 20      // (mm/s) Z axis feedrate (not used for delta printers)
#define PRINTJOB_TIMER_AUTOSTART
#define LCD_LANGUAGE en
#define DISPLAY_CHARSET_HD44780 JAPANESE
#define LCD_INFO_SCREEN_STYLE 0
#define SDSUPPORT
#define ENCODER_PULSES_PER_STEP 2
#define ENCODER_STEPS_PER_MENU_ITEM 2
#define INDIVIDUAL_AXIS_HOMING_MENU
#define LCD_FEEDBACK_FREQUENCY_DURATION_MS 2
#define LCD_FEEDBACK_FREQUENCY_HZ 4200
#define LCD_I2C_PANELOLU2
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

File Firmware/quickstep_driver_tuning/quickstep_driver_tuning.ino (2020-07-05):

/*
   Program that runs diagnostic tests for QuickStep
   What we want it to do:

   ===== IN SETUP =====
    x check if motor power good is LOW when the power supply is off
    x check if we get ACKs at EEPROM_ADDR and LCD_ADDR
    x turn the supply on
    x check if motor power good is HIGH when the power supply is on
    - initialize the Trinamic Drivers
    x read address 0,
    x- if the read value is 0, write a value to it
    x- read the value that we wrote to address 0

   ===== IN LOOP =====
    Every 250ms;
     x send XYZFil sensor status to serial monitor
     x send the thermistor resistance
     x send the value of the card detect line
     - diagnostic lines of the trinamic drivers?
     x increment a 3-bit counter that rolls over

    Every 500ms:
     x toggle print cooling fan

    Every 10ms:
      x Read the encoder pins
      x Update the encoder value

    x Run the RGB LED according to the 3-bit counter
    x Set the direction of the drivers to the top bit of the counter
    Step motor every millisecond

*/
#include <Wire.h>
#include <SPI.h>
#include <LiquidTWI2.h>
#include <TMCStepper.h>
#include <DueTimer.h>

#include "pins.h"

#define LCD_ADDR 0x20
#define EEPROM_ADDR 0x50
#define EEPROM_WRITE_VAL 0xAA

#define AREAD_BITS 12
#define PULLUP (float)4700

unsigned long counter = 0;
uint8_t minicount = 0;
uint8_t lcd_counter = 0;

long enc_count = 0;
bool a_past, c_past;

LiquidTWI2 lcd(LCD_ADDR);

#define R_SENSE 0.11f
#define T_BLANK 36
#define T_OFF 4
#define HYST_START 2
#define HYST_END 3
TMC2130Stepper axis_x(X_CS, R_SENSE);
TMC2130Stepper axis_y(Y_CS, R_SENSE);
TMC2130Stepper axis_z(Z_CS, R_SENSE);
TMC2130Stepper axis_e(E_CS, R_SENSE);

#define FREQ_MIN 1000
#define FREQ_MAX 128000
uint32_t step_freq = FREQ_MIN;

volatile uint32_t step_count;
#define STEP_LIMIT 320000

struct {
  uint8_t blank_time = 24;        // [16, 24, 36, 54]
  uint8_t off_time = 4;           // [1..15]
  uint8_t hysteresis_start = 6;   // [1..8]
  int8_t hysteresis_end = 12;     // [-3..12]
} config;

void reportCurrentSettings() {
  Serial.print("Off time = ");
  Serial.print(config.off_time);
  Serial.print(" Hysteresis end = ");
  Serial.print(config.hysteresis_end);
  Serial.print(" Hysteresis start = ");
  Serial.println(config.hysteresis_start);
}

void step_motor() {
  digitalWrite(X_STEP, HIGH);
  //delayMicroseconds(5);
  digitalWrite(X_STEP, LOW);
  step_count++;
  if(step_count > STEP_LIMIT) { TOGGLE(X_DIR); step_count = 0;}
}

void eeprom_read_test() {
  Wire1.beginTransmission(EEPROM_ADDR);
  Wire1.write(0);
  Wire1.write(0);
  Wire1.endTransmission();
  Wire1.requestFrom(EEPROM_ADDR, 1);
  while (!Wire1.available());
  byte recv;
  recv = Wire1.read();
  if (recv == EEPROM_WRITE_VAL) {
    Serial.print("Received " + (String)recv);
    Serial.println(" Success");
    return;
  }
  Serial.println("Received " + (String)recv + ", retesting after write");
  Wire1.beginTransmission(EEPROM_ADDR);
  Wire1.write(0);
  Wire1.write(0);
  Wire1.write(EEPROM_WRITE_VAL); //10101010
  Wire1.endTransmission();
  Serial.println(F("Writing 0xAA to Address 0x00"));
  Serial.print(F("Retrying Read..."));
  eeprom_read_test();
}

void setup() {
  Serial.begin(250000);
  Serial.println();
  Serial.println();
  Serial.println(F("Quickstep Diagnostic"));
  Serial.print(F("Initializing GPIO..."));
  pins_init();
  analogReadResolution(AREAD_BITS);
  delay(500);
  Serial.println(F("Success"));

  Serial.print(F("Initializing I2C Bus..."));
  Wire1.begin();
  Wire1.setClock(100000);
  delay(500);
  Serial.println(F("Success"));

  Serial.print("Testing address of EEPROM: " + (String)EEPROM_ADDR + "...");
  do {
    delay(500);
    Serial.print(".");
    Wire1.beginTransmission(EEPROM_ADDR);
  } while (Wire1.endTransmission() != 0);
  Serial.println(F("Success"));

  Serial.print(F("EEPROM Read Test..."));
  eeprom_read_test();


  Serial.print("Testing address of LCD: " + (String)LCD_ADDR + "...");
  do {
    delay(500);
    Serial.print(".");
    Wire1.beginTransmission(LCD_ADDR);
  } while (Wire1.endTransmission() != 0);
  Serial.println(F("Success"));


  lcd.setMCPType(LTI_TYPE_MCP23017);
  lcd.begin(20, 4);
  lcd.print("     Quickstep      ");
  lcd.setCursor(0, 1);
  lcd.print("     Diagnostic     ");
  lcd.setCursor(0, 2);
  lcd.print("Encoder Count: 0    ");
  lcd.setCursor(0, 3);
  lcd.print("Click to Reset Count");
  SETHIGH(LED_RED);
  SETHIGH(LED_GREEN);
  SETHIGH(LED_BLUE);
  delay(500);

  Serial.print(F("Power Good Status..."));
  if (!READ(VMOT_GOOD)) {
    Serial.println(F("FAILED"));
    while (true);
  }
  Serial.println(F("Not Good...OK"));
  delay(500);
  Serial.println("Turning on supply...");
  SETHIGH(PS_ON);
  delay(500);
  Serial.print(F("Power Good Status..."));
  if (READ(VMOT_GOOD)) {
    Serial.println(F("FAILED"));
    while (true);
  }
  Serial.println(F("Good"));


  Serial.println(F("Initializing Steppers..."));
  Serial.print(F("\tAxis X..."));
  SPI.begin();
  //SPI.setClockDivider(84);
  if (axis_x.test_connection()) {
    Serial.print(F("FAILED - Error Code: "));
    Serial.println(axis_x.test_connection());
    //while(true);
  }
  axis_x.push();
  axis_x.blank_time(T_BLANK);
  axis_x.toff(T_OFF);
  axis_x.hysteresis_start(HYST_START);
  axis_x.hysteresis_end(HYST_END);
  axis_x.microsteps(256);
  axis_x.en_pwm_mode(false);
  axis_x.rms_current(750);

  Serial.println(F("Success"));
  Serial.print(F("\tAxis Y..."));
  SPI.begin();
  //SPI.setClockDivider(84);
  if (axis_y.test_connection()) {
    Serial.print(F("FAILED - Error Code: "));
    Serial.println(axis_y.test_connection());
    //while(true);
  }
  axis_y.push();
  axis_y.blank_time(T_BLANK);
  axis_y.toff(T_OFF);
  axis_y.hysteresis_start(HYST_START);
  axis_y.hysteresis_end(HYST_END);
  axis_y.microsteps(32);
  axis_y.en_pwm_mode(true);
  axis_y.rms_current(1000);

  Serial.println(F("Success"));
  Serial.print(F("\tAxis Z..."));
  SPI.begin();
  //SPI.setClockDivider(84);
  if (axis_z.test_connection()) {
    Serial.print(F("FAILED - Error Code: "));
    Serial.println(axis_z.test_connection());
    //while(true);
  }
  axis_z.push();
  axis_z.blank_time(T_BLANK);
  axis_z.toff(T_OFF);
  axis_z.hysteresis_start(HYST_START);
  axis_z.hysteresis_end(HYST_END);
  axis_z.microsteps(32);
  axis_z.en_pwm_mode(true);
  axis_z.rms_current(1000);

  Serial.println(F("Success"));
  Serial.print(F("\tAxis E..."));
  SPI.begin();
  //SPI.setClockDivider(84);
  if (axis_e.test_connection()) {
    Serial.print(F("FAILED - Error Code: "));
    Serial.println(axis_e.test_connection());
    //while(true);
  }
  Serial.println(F("Success"));
  axis_e.push();
  axis_e.blank_time(T_BLANK);
  axis_e.toff(T_OFF);
  axis_e.hysteresis_start(HYST_START);
  axis_e.hysteresis_end(HYST_END);
  axis_e.microsteps(32);
  axis_e.en_pwm_mode(true);
  axis_e.rms_current(1000);


  SETLOW(X_EN);
  SETLOW(Y_EN);
  SETLOW(Z_EN);
  SETLOW(E_EN);

  Serial.print(F("Setting driver blank time to "));
  Serial.print(config.blank_time);
  Serial.println(F(" cycles."));
  axis_x.blank_time(config.blank_time);

  Serial.print(F("Setting driver off time to "));
  Serial.println(config.off_time);
  axis_x.toff(config.off_time);

  Serial.print(F("Setting hysteresis end value to "));
  Serial.println(config.hysteresis_end);
  axis_x.hysteresis_end(config.hysteresis_end);

  Serial.print(F("Setting hysteresis start value to "));
  Serial.println(config.hysteresis_start);
  axis_x.hysteresis_start(config.hysteresis_start);

  Serial.println(F("Starting Loop..."));

}

void loop() {
  if (Serial.available() > 0) {
    DueTimer myTimer = Timer.getAvailable();
    myTimer.attachInterrupt(step_motor);
    myTimer.setFrequency(step_freq);
    myTimer.start();

    uint8_t c = Serial.read();
    if (c == '+') {
      if (config.hysteresis_end == 12) Serial.println(F("Reached MAX setting already!"));
      else {
        config.hysteresis_end++;
        reportCurrentSettings();
        axis_x.hysteresis_end(config.hysteresis_end);
      }
    } else if (c == '-') {
      if (config.hysteresis_end == -3) Serial.println(F("Reached MIN setting already!"));
      else {
        config.hysteresis_end--;
        reportCurrentSettings();
        axis_x.hysteresis_end(config.hysteresis_end);
      }
    } else if (c == 'u') {
      if (step_freq < FREQ_MAX) {
        step_freq = step_freq << 1;
        Serial.print("Increasing Stepping Frequency to ");
        Serial.println(step_freq);
        myTimer.setFrequency(step_freq);
      }
      else Serial.println("Stepping Freq at its Max");
    } else if (c == 'd') {
      if (step_freq > FREQ_MIN) {
        step_freq = step_freq >> 1;
        Serial.print("Decreasing Stepping Frequency to ");
        Serial.println(step_freq);
        myTimer.setFrequency(step_freq);
      }
      else Serial.println("Stepping Freq at its Min");
    }
    else if (c == '=') {
      Serial.print(F("Final effective hysteresis = "));
      Serial.print(config.hysteresis_end);
      Serial.print(F(" + "));
      Serial.print(config.hysteresis_start);
      Serial.print(F(" = "));
      Serial.println(config.hysteresis_end + config.hysteresis_start);
      Serial.println(F("Your configuration parameters in Marlin are:"));
      Serial.print(F("#define CHOPPER_TIMING "));
      Serial.print(config.off_time);
      Serial.print(F(" "));
      Serial.print(config.hysteresis_end);
      Serial.print(F(" "));
      Serial.print(config.hysteresis_start);
      abort();
    }
  }
}

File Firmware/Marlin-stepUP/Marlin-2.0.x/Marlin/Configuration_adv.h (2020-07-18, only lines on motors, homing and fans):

#define E0_AUTO_FAN_PIN -1
#define E1_AUTO_FAN_PIN -1
#define E2_AUTO_FAN_PIN -1
#define E3_AUTO_FAN_PIN -1
#define E4_AUTO_FAN_PIN -1
#define E5_AUTO_FAN_PIN -1
#define CHAMBER_AUTO_FAN_PIN -1
#define X_HOME_BUMP_MM 5
#define Y_HOME_BUMP_MM 5
#define Z_HOME_BUMP_MM 2
#define HOMING_BUMP_DIVISOR { 2, 2, 4 }  // Re-Bump Speed Divisor (Divides the Homing Feedrate)
#define QUICK_HOME                     // If homing includes X and Y, do a diagonal move initially
#define MICROSTEP_MODES { 16, 16, 16, 16, 16, 16 } // [1,2,4,8,16]
#define DIGIPOT_I2C_MOTOR_CURRENTS { 1.0, 1.0, 1.0, 1.0, 1.0, 1.0, 1.0, 1.0 }  //  AZTEEG_X3_PRO
#define LIN_ADVANCE
  #define LIN_ADVANCE_K 0.04    // Unit: mm compression per 1mm/s extruder speed
#define ADVANCED_PAUSE_FEATURE
  #define ADVANCED_PAUSE_CONTINUOUS_PURGE       // Purge continuously up to the purge length until interrupted.
  #define ADVANCED_PAUSE_PURGE_FEEDRATE        3  // (mm/s) Extrude feedrate (after loading). Should be slower than load feedrate.
  #define ADVANCED_PAUSE_PURGE_LENGTH        500  // (mm) Length to extrude after loading.
  #define ADVANCED_PAUSE_RESUME_PRIME          0  // (mm) Extra distance to prime nozzle after returning from park.
  #define ADVANCED_PAUSE_FANS_PAUSE             // Turn off print-cooling fans while the machine is paused.
    #define X_CURRENT       650        // (mA) RMS current. Multiply by 1.414 for peak current.
    #define X_CURRENT_HOME  X_CURRENT  // (mA) RMS current for sensorless homing
    #define X_MICROSTEPS     16    // 0..256
    #define Y_CURRENT       1050
    #define Y_CURRENT_HOME  Y_CURRENT
    #define Y_MICROSTEPS     16
    #define Z_CURRENT       400
    #define Z_CURRENT_HOME  Z_CURRENT
    #define Z_MICROSTEPS     16
    #define E0_CURRENT      800
    #define E0_MICROSTEPS    16
    #define CURRENT_STEP_DOWN     50  // [mA]
    #define REPORT_CURRENT_CHANGE
  #define X_HYBRID_THRESHOLD     100  // [mm/s]
  #define X2_HYBRID_THRESHOLD    100
  #define Y_HYBRID_THRESHOLD     100
  #define Y2_HYBRID_THRESHOLD    100
  #define Z_HYBRID_THRESHOLD       3
  #define Z2_HYBRID_THRESHOLD      3
  #define Z3_HYBRID_THRESHOLD      3
  #define Z4_HYBRID_THRESHOLD      3
  #define E0_HYBRID_THRESHOLD     30
  #define E1_HYBRID_THRESHOLD     30
  #define E2_HYBRID_THRESHOLD     30
  #define E3_HYBRID_THRESHOLD     30
  #define E4_HYBRID_THRESHOLD     30
  #define E5_HYBRID_THRESHOLD     30
  #define E6_HYBRID_THRESHOLD     30
  #define E7_HYBRID_THRESHOLD     30

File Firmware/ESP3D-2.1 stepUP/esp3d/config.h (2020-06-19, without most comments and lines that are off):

#define FW_VERSION "2.1.0.b39"
#define REPOSITORY "https://github.com/luc-github/ESP3D"
#define ESP8266_MODEL_NAME "ESP8266"
#define ESP8266_MODEL_URL "http://espressif.com/en/products/esp8266/"
#define ESP32_MODEL_NAME "ESP32"
#define ESP32_MODEL_URL "https://www.espressif.com/en/products/hardware/esp-wroom-32/overview"
#define ESP_MODEL_NUMBER "ESP3D 2.1"
#define ESP_MANUFACTURER_NAME "Espressif Systems"
#define ESP_MANUFACTURER_URL "http://espressif.com"
#define ESP_DEFAULT_NAME "stepup"
#define ESP_HOST_NAME ESP_DEFAULT_NAME
#define SERIAL_COMMAND_FEATURE
#define TCP_IP_DATA_FEATURE
#define NOTIFICATION_FEATURE
#define MDNS_FEATURE
#define SSDP_FEATURE
#define NETBIOS_FEATURE
#define CAPTIVE_PORTAL_FEATURE
#define WEB_UPDATE_FEATURE
#define DIRECT_PIN_FEATURE
#define WS_DATA_FEATURE
#define SERIAL_RX_BUFFER_SIZE 512
#define ESP_SERIAL_PARAM SERIAL_8N1
#define USE_SERIAL_2
#define ESP_RX_PIN -1
#define ESP_TX_PIN -1
#define SD_PWR_PIN 19
#define SD_SWITCH_PIN 18
#define SD_CS_SENSE_PIN 21
#define SD_CD_PIN 5
#define UNKNOWN_FW 0
#define REPETIER4DV	1
#define MARLIN		2
#define MARLINKIMBRA		3
#define SMOOTHIEWARE	4
#define REPETIER		5
#define GRBL		6
#define MAX_FW_ID 6
#define ESP_USE_ASYNC false
#define MAX_SRV_CLIENTS 1
#ifdef ARDUINO_ARCH_ESP32
#include "FS.h"
#include "SPIFFS.h"
using fs::File;
#define WIFI_NONE_SLEEP WIFI_PS_NONE
#define WIFI_LIGHT_SLEEP WIFI_PS_MIN_MODEM
#define WIFI_MODEM_SLEEP WIFI_PS_MAX_MODEM
#define WIFI_PHY_MODE_11B WIFI_PROTOCOL_11B
#define WIFI_PHY_MODE_11G WIFI_PROTOCOL_11B | WIFI_PROTOCOL_11G
#define WIFI_PHY_MODE_11N WIFI_PROTOCOL_11B | WIFI_PROTOCOL_11G | WIFI_PROTOCOL_11N
#define AUTH_OPEN WIFI_AUTH_OPEN
#define AUTH_WEP WIFI_AUTH_WEP
#define AUTH_WPA_PSK WIFI_AUTH_WPA_PSK
#define AUTH_WPA2_PSK WIFI_AUTH_WPA2_PSK
#define AUTH_WPA_WPA2_PSK WIFI_AUTH_WPA_WPA2_PSK
#define ENC_TYPE_NONE AUTH_OPEN
#define FS_FILE File
#define FS_DIR File
#define SD_FILE_READ FILE_READ
#define SPIFFS_FILE_READ FILE_READ
#define SD_FILE_WRITE FILE_WRITE
#define SPIFFS_FILE_WRITE FILE_WRITE
#define WIFI_EVENT_STAMODE_CONNECTED SYSTEM_EVENT_STA_CONNECTED
#define WIFI_EVENT_STAMODE_DISCONNECTED SYSTEM_EVENT_STA_DISCONNECTED
#define WIFI_EVENT_STAMODE_GOT_IP SYSTEM_EVENT_STA_GOT_IP
#define WIFI_EVENT_SOFTAPMODE_STACONNECTED SYSTEM_EVENT_AP_STACONNECTED
#else
#define FS_DIR fs::Dir
#define FS_FILE fs::File
#define SD_FILE_READ FILE_READ
#define SPIFFS_FILE_READ "r"
#define SD_FILE_WRITE FILE_WRITE
#define SPIFFS_FILE_WRITE "w"
#endif
#define LOG(string) {}
#define DEBUG_PIPE NO_PIPE
#define NOLOG(string) {}
#define CONFIG_h
#include <Arduino.h>
#ifdef ARDUINO_ARCH_ESP8266
extern "C" {
#include "user_interface.h"
}
#else
#endif
#include "wificonf.h"
typedef enum {
    UPLOAD_STATUS_NONE = 0,
    UPLOAD_STATUS_FAILED = 1,
    UPLOAD_STATUS_CANCELLED = 2,
    UPLOAD_STATUS_SUCCESSFUL = 3,
    UPLOAD_STATUS_ONGOING  = 4
} upload_status_type;
typedef enum {
    NO_PIPE = 0,
    SERIAL_PIPE = 2,
    SERIAL1_PIPE = 3,
    SERIAL2_PIPE = 4,
    TCP_PIPE = 5,
    WS_PIPE = 6,
    WEB_PIPE = 8,
    PRINTER_PIPE = 9
} tpipe;
#define DEFAULT_PRINTER_PIPE SERIAL_PIPE
typedef enum {
    LEVEL_GUEST = 0,
    LEVEL_USER = 1,
    LEVEL_ADMIN = 2
} level_authenticate_type;
#define    NO_SD 0
#define    SD_DIRECTORY 1
#define    EXT_DIRECTORY 2
#define AP_MODE			1
#define CLIENT_MODE		2
#define DHCP_MODE		1
#define STATIC_IP_MODE		2
#define EP_WIFI_MODE			0    //1 byte = flag
#define EP_STA_SSID				1    //33 bytes 32+1 = string  ; warning does not support multibyte char like chinese
#define EP_STA_PASSWORD			34   //65 bytes 64 +1 = string ;warning does not support multibyte char like chinese
#define EP_STA_IP_MODE			99   //1 byte = flag
#define EP_STA_IP_VALUE			100  //4  bytes xxx.xxx.xxx.xxx
#define EP_STA_MASK_VALUE			104  //4  bytes xxx.xxx.xxx.xxx
#define EP_STA_GATEWAY_VALUE			108  //4  bytes xxx.xxx.xxx.xxx
#define EP_BAUD_RATE			112  //4  bytes = int
#define EP_STA_PHY_MODE			116  //1 byte = flag
#define EP_SLEEP_MODE			117  //1 byte = flag
#define EP_CHANNEL			118 //1 byte = flag
#define EP_AUTH_TYPE			119 //1 byte = flag
#define EP_SSID_VISIBLE			120 //1 byte = flag
#define EP_WEB_PORT			121 //4  bytes = int
#define EP_DATA_PORT			125 //4  bytes = int
#define EP_OUTPUT_FLAG			129 //1  bytes = flag
#define EP_HOSTNAME				130//33 bytes 32+1 = string  ; warning does not support multibyte char like chinese
#define EP_DHT_INTERVAL		    164//4  bytes = int
#define ESP_NOTIFICATION_TYPE   168     //1 byte = flag
#define ESP_AUTO_NOTIFICATION   170//1  bytes = flag
#define EP_FREE_BYTE1		    171//1  bytes = flag
#define EP_FREE_INT3		    172//4  bytes = int
#define EP_ADMIN_PWD		    176//21  bytes 20+1 = string  ; warning does not support multibyte char like chinese
#define EP_USER_PWD		    197//21  bytes 20+1 = string  ; warning does not support multibyte char like chinese
#define EP_AP_SSID				218    //33 bytes 32+1 = string  ; warning does not support multibyte char like chinese
#define EP_AP_PASSWORD			251   //65 bytes 64 +1 = string ;warning does not support multibyte char like chinese
#define EP_AP_IP_VALUE			316  //4  bytes xxx.xxx.xxx.xxx
#define EP_AP_MASK_VALUE			320  //4  bytes xxx.xxx.xxx.xxx
#define EP_AP_GATEWAY_VALUE			324  //4  bytes xxx.xxx.xxx.xxx
#define EP_AP_IP_MODE			329   //1 byte = flag
#define EP_AP_PHY_MODE			330  //1 byte = flag
#define EP_SD_SPEED_DIV			331  //1 byte = flag
#define ESP_NOTIFICATION_TOKEN1 332    //64 bytes 63+1 = string  ; warning does not support multibyte char like chinese
#define ESP_NOTIFICATION_TOKEN2 396    //64 bytes 63+1 = string  ; warning does not support multibyte char like chinese
#define EP_DHT_TYPE		460 //1  bytes = flag
#define EP_TARGET_FW		461 //1  bytes = flag
#define EP_TIMEZONE         462//1  bytes = flag
#define EP_TIME_ISDST       463//1  bytes = flag
#define EP_TIME_SERVER1 464//129 bytes 128+1 = string  ; warning does not support multibyte char like chinese
#define EP_TIME_SERVER2  593 //129 bytes 128+1 = string  ; warning does not support multibyte char like chinese
#define EP_TIME_SERVER3  722 //129 bytes 128+1 = string  ; warning does not support multibyte char like chinese
#define EP_IS_DIRECT_SD   850//1  bytes = flag
#define EP_PRIMARY_SD   851//1  bytes = flag
#define EP_SECONDARY_SD   852//1  bytes = flag
#define EP_DIRECT_SD_CHECK   853//1  bytes = flag
#define EP_SD_CHECK_UPDATE_AT_BOOT   854//1  bytes = flag
#define ESP_NOTIFICATION_SETTINGS 855//128 bytes 127+1 = string  ; warning does not support multibyte char like chinese
#define EP_EEPROM_VERSION 1017// 6 bytes = ESP3D<V on one byte>
#define LAST_EEPROM_ADDRESS 983
#define DEFAULT_WIFI_MODE			AP_MODE
const char DEFAULT_AP_SSID []  PROGMEM =		"ESP3D";
const char DEFAULT_AP_PASSWORD [] PROGMEM =	"12345678";
const char DEFAULT_STA_SSID []  PROGMEM =		"ESP3D";
const char DEFAULT_STA_PASSWORD [] PROGMEM =	"12345678";
const byte DEFAULT_STA_IP_MODE  = 				DHCP_MODE;
const byte DEFAULT_AP_IP_MODE = 				STATIC_IP_MODE;
const byte DEFAULT_IP_VALUE[]   =	        {192, 168, 0, 1};
const byte DEFAULT_MASK_VALUE[]  =	        {255, 255, 255, 0};
#define DEFAULT_GATEWAY_VALUE   	        DEFAULT_IP_VALUE
const long DEFAULT_BAUD_RATE =			250000;
#define DEFAULT_PHY_MODE			WIFI_PHY_MODE_11G
#define DEFAULT_SLEEP_MODE			WIFI_MODEM_SLEEP
#define DEFAULT_CHANNEL				11
#define DEFAULT_AUTH_TYPE			AUTH_WPA_PSK
#define DEFAULT_SSID_VISIBLE			1
#define DEFAULT_MAX_CONNECTIONS			4
#define DEFAULT_BEACON_INTERVAL			100
const int DEFAULT_WEB_PORT =			80;
const int DEFAULT_DATA_PORT =			8888;
const char DEFAULT_ADMIN_PWD []  PROGMEM =	"admin";
const char DEFAULT_USER_PWD []  PROGMEM =	"user";
const char DEFAULT_ADMIN_LOGIN []  PROGMEM =	"admin";
const char DEFAULT_USER_LOGIN []  PROGMEM =	"user";
const char DEFAULT_TIME_SERVER1 []  PROGMEM =	"1.pool.ntp.org";
const char DEFAULT_TIME_SERVER2 []  PROGMEM =	"2.pool.ntp.org";
const char DEFAULT_TIME_SERVER3 []  PROGMEM =	"0.pool.ntp.org";
#define DEFAULT_TIME_ZONE			0
#define DEFAULT_TIME_DST			0
#define DEFAULT_PRIMARY_SD  2
#define DEFAULT_SECONDARY_SD 1
#define DEFAULT_DIRECT_SD_CHECK 0
#define DEFAULT_SD_CHECK_UPDATE_AT_BOOT 1
#define DEFAULT_OUTPUT_FLAG 0
#define DEFAULT_DHT_TYPE 255
const int DEFAULT_DHT_INTERVAL = 30;
#define MIN_NOTIFICATION_TOKEN_LENGTH 0
#define MIN_NOTIFICATION_SETTINGS_LENGTH 0
#define MAX_NOTIFICATION_TOKEN_LENGTH 63
#define MAX_NOTIFICATION_SETTINGS_LENGTH 127
#define DEFAULT_NOTIFICATION_TYPE 0
#define DEFAULT_NOTIFICATION_TOKEN1 ""
#define DEFAULT_NOTIFICATION_TOKEN2 ""
#define DEFAULT_NOTIFICATION_SETTINGS ""
#define DEFAULT_AUTO_NOTIFICATION_STATE 1
#define NOTIFICATION_ESP_ONLINE "Hi, %ESP_NAME% is now online at %ESP_IP%"
#define ESP_PUSHOVER_NOTIFICATION	1
#define ESP_EMAIL_NOTIFICATION		2
#define ESP_LINE_NOTIFICATION		3
#ifdef SDCARD_FEATURE
#define DEFAULT_IS_DIRECT_SD 1
#else
#define DEFAULT_IS_DIRECT_SD 0
#endif
#ifdef ARDUINO_ARCH_ESP8266
#define DEFAULT_SDREADER_SPEED 2
#else
#define DEFAULT_SDREADER_SPEED 4
#endif
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

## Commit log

2020-06-04 Reuploading Entire Repo
    [ATX_Connections.sch, Boost MOSFET Dissipation Calcs.xlsx, Configuration.h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]
2020-06-16 Removing ESP3D v3, Fixing display throtting issues for Marlin
    [Configuration.h, Configuration_adv.h, configuration.h]
2020-06-19 Messing around with direct SD-MMC upload; hardware changes required and messing around with ESP3D
    [ATX_Connections.sch, Configuration.h, qs_Drivers.sch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]
2020-07-05 Adding Quickstep diagnostic test, and messing around with Trinamic driver settings
    [Configuration.h, Configuration_adv.h]
2020-07-09 Changes for V6 Hotend, messing around with cold pull script, minor bugfix for unload
    [Configuration.h, Configuration_adv.h]
2020-07-18 Removing filament unload from LCD Menu, swapping to classic jerk for extruder jerk control
    [Configuration.h, Configuration_adv.h]
2024-07-20 Including copy of LiquidTWI2 and some minor Marlin changes to get stepUP working again
    [Configuration.h]

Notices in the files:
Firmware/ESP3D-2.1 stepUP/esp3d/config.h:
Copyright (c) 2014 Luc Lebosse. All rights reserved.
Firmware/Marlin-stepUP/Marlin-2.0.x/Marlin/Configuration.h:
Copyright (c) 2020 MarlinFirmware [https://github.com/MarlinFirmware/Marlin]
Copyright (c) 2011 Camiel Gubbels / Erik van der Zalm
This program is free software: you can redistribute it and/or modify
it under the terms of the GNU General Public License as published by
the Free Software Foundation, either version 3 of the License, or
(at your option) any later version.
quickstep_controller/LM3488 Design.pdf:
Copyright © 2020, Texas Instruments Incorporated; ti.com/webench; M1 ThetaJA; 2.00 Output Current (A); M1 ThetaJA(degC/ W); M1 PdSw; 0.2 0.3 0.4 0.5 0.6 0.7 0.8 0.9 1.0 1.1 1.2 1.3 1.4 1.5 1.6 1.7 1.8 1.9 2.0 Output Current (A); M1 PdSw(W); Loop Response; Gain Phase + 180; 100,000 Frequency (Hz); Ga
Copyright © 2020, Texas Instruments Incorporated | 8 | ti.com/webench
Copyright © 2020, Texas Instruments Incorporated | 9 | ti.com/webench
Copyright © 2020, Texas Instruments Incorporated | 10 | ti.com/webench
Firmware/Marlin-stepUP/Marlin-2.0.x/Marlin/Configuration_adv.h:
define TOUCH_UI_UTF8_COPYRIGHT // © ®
